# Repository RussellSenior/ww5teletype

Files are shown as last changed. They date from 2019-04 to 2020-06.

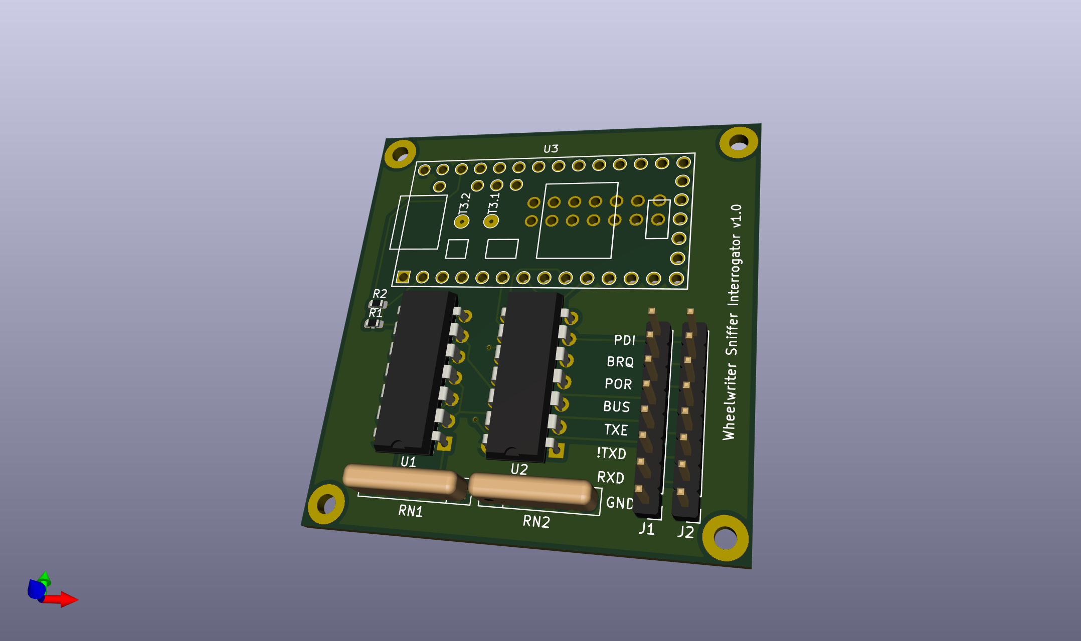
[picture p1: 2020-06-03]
hardware/reverse-engr/reverse-engr.png

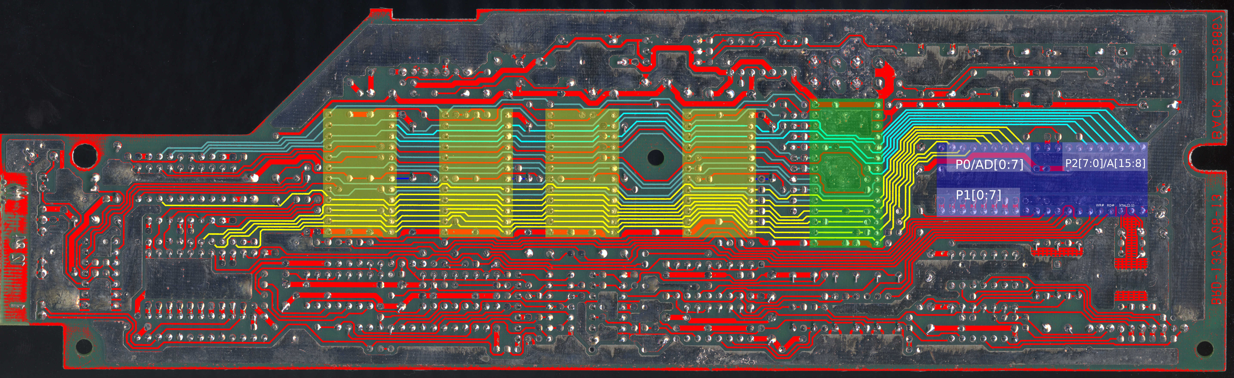
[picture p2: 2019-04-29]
img/wheelwriter_5_pcb_tracing_in_progress.jpg

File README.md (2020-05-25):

Exploration of the IBM Wheelwriter 5

This is a project motivated by a desire to create a daisywheel teletype, to give a 
similar experience to that of a Model 33ASR teletype, but with upper and lowercase 
characters. Thanks to Hugh Pyle and his fantastic [Twitch channel](https://www.twitch.tv/33asr) for the 
inspiration.  Thanks also to Chris Gregg and his project:
https://github.com/tofergregg/IBM-Wheelwriter-Hack and to this very similar project 
by Stephen Casner: https://github.com/IBM-1620/Junior.

The goal is to intercept user input from the keyboard and send it to a remote computer
and receive the echoed characters from the remote computer and send the corresponding
commands to the printing mechanism for hardcopy output.

I obtained an IBM Wheelwriter 5 from the Tektronix Surplus Store (open two days a month,
first and third Thursdays, from 2pm to 4pm) on the Beaverton Oregon campus of Tektronix. 
This typewriter came with the parallel port option, which hangs on the back of the case
and interfaces by a 6 (or 7?) pin bus. The cost of the typewriter was $25. I purchased 
two new-in-box ribbon cartridges from the same location for $0.50 each.

Following the lead of Chris Gregg, I began by putting a logic analyzer on the "bus" pin
between the keyboard controller board near the front of the typewriter and the motor 
control board in the rear of the typewriter and watching the response to keystrokes.

The keyboard controller board uses an Intel 8031 (romless version of the venerable 8051).
Reading the MCS-51 MICROCONTROLLER FAMILY USER’S MANUAL from Intel, it appears that the 
interboard communication takes place using a UART signaling but with the wrinkle that
both transmit and receive occur on the same wire. It appears that the UART is placed in 
the so-called "mode 2", which uses a 9-bit message, lsb first, where a one in the ninth bit 
indicates a corresponding target device (specified by the normal 8 bits) on the bus should 
listen to the message. Each message is ACK'd with nine bits of zero, presumably by the 
target device. Communication is at 1/64 of the crystal oscillator speed of 12MHz, which 
works out to 187500 baud (the logic analyzer, a Saleae clone using pulseview of the Sigrok
project, estimated the baud rate was 187060, which is very close, within 1/4%).

My original plan was to man-in-the-middle this serial bus wire, intercepting the commands 
coming from the keyboard controller board, decoding them, and sending a corresponding 
ASCII character (or, perhaps, string) to the remote computer over a normal 8N1 like UART,
receiving a ASCII back from the remote computer and injecting the corresponding commands
on the split bus.  However, due to some challenges, this is easier said than done:

Amongst other things, the keyboard has no "Control" key, therefore it becomes necessary
to hijack another key to act on its behalf. The most obvious candidate is the "Code"
key, which sits on the space bar row, to the left of the space bar. The difficulty arises
when you discover that the combination of "Code" and some other keys generates a rather 
complex series of commands, which would need to be decoded. This isn't impossible, but it
seems like a lot of complex work.

A second alternative, one taken by Stephen Casner for the IBM 1620 Junior project, is to 
intercept key presses directly from the FFC cables coming from the keyboard itself, and decode
the matrix. The corresponding ASCII characters can be sent to the remote computer and a fake
keyboard can be presented to the keyboard controller board.  I need to learn more about how
the keyboard matrix works.

One desirable feature is the ability to return to a "local" (vs "line") mode, where normal
typewriter functionality is restored, either through software or perhaps a hardware switch.

Thanks to the able assistance of [Jared Boone](https://github.com/jboone) of [ShareBrained Technology](https://www.sharebrained.com/), of Chronulator and 
PortaPack fame, I was able to obtain dumps of the off-chip ROMs for the keyboard controller 
and printer option boards (there are some other ROMs, but they seem less important).  They
can be found in the rom subdirectory. The motor control ROM would also be interesting, but
they are more obfuscated than even the keyboard controller board.

One oddity found in the disassembled firmware so far, it's not clear where the UART is 
configured in the keyboard controller firmware. I see references to the control register 
SCON in the printer board firmware, but not in the keyboard controller. Setting up the 
9-bit serial mode must require twiddling that register, so wtf?

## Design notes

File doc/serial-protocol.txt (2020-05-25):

There is a ribbon cable connecting the function board in front to the printer board in back. The pins are labelled (left to right):

 * +12
 * PDI
 * BRQ
 * BUS
 * GND
 * POR
 * +5

+12 carries a 12V supply, and +5 carries a 5V supply. GND is Ground. So much for the obvious. BUS carries serial communication between the boards. POR is Power On Reset, is low for a while at power on while things are initialized. BRQ is probably Bus Request. It is only asserted (LOW) when the PC Printer Option is attached, and only when the 0x140 byte is transmitted. PDI is a complete mystery so far.

The printer board also has a 0.1-inch pin header for connecting an external option card. In my case, I have a PC Printer Option card that came with the typewriter. The pins on this connector are labelled:

 * +5
 * GND
 * BUS
 * BRQ
 * POR
 * +34
 * PDI

Observations:

 * The protocol on the BUS wire is a 9-bit serial, apparently the so-called "mode 2" referred to in the Intel 8051 documentation: http://datasheets.chipdb.org/Intel/MCS51/MANUALS/27238302.PDF
 * The 9-bit bytes with the most-significant bit set indicate that the remaining bits are a processor address intended to listen to the commands that follow, so the many 0x121 are just spamming an announcement that the microprocessor on the bus that thinks of itself as 0x21 should pay attention, and that other microprocessors can sleep (only looking for the most-significant bit to see if they should check the address again). One can reasonably deduce that 0x21 is the address of the motor controller board. All other bytes, where the 9th bit is not set, are commands or arguments.
 * horizontal motion is typically measured in microsteps, 1/120th of an inch;
 * carriage motion is most often commanded relative to the current position, so it is necessary for the programming issuing commands to maintain a notion of where the carriage is located for carriage returns and to prevent venturing off the right end;
 * 0x03 takes two arguments, the first byte being the absolute rotation of the daisy wheel (between 0 and 0x60, inclusive) to strike, and the second byte being the number of microsteps to move the carriage to the right afterwards;
 * 0x04 seems to be similar to 0x03, except that it causes the ribbon positioning motor to rotate the rubout tape into position to be struck instead of the normal ribbon;
 * 0x05 command is a platen positioning command, the most significant bit of the single byte argument is a direction bit (1 for up, 0 for down), the rest indicate the magnitude of motion in 1/96ths of an inch;
 * 0x06 command is a carriage positioning command, taking two byte arguments: the most significant bit of the first byte indicates the direction (1 to move the carriage right, 0 to move the carriage to the left), the remaining bits indicate the number of microsteps (1/120th of an inch) to move horizontally;
 * 0x09 command followed by the single byte argument 0x04 seems to turn on underlining;
 * 0x09 command followed by the single byte argument 0x00 seems to turn off underlining;
 * 0x0B commands seem to not result in any actions, maybe a "rest" or "request status" command (we sometimes see non-zero replies to it);
 * 0x0C commands appear after a rubout operation;
 * 0x0D commands appear in connection with:
  * 0x05 during rubout;
  * 0x04 during backspace;
  * 0x07 during carriage return;
  * 0x0a during tab resolution;
  * 0x12 during tab set;
 * 0x0E commands appear in association with "code" related key presses;

 * A carriage return with a Courier 15 printwheel installed emitted an argument of 0x0c (decimal 12), which equates to 8 lines per inch. I also discovered that after an 0x03 command (i.e. printing/advancing), another addressing byte (0x121) was needed before a 0x05 (or probably any other command) was recognized or acknowledged.

 * With the PC Printer option attached, after putting the wheelwriter into Printer On mode (which is associated with its own bus traffic), sending data from a PC over /dev/usb/lp1 (which is line buffered and isn't printed until a ^M is sent), I see the following sequence:
  * about 16.8us before the first character, BRQ is pulled low, then the 9-bit character 0x140 appears;
  * about 87.5us after the start bit, BRQ is deasserted (goes HI again);
  * generally speaking BRQ going LO seems to be associated with the 0x140 byte generally, sometimes including other bytes.
  * as mentioned above the high bit being set implies an address in the lower 8 bits, in this case 0x40;
  * 0x114 appears (unless otherwise indicated, 0x00 replies are implied);
  * 0x005;
  * 0x006;
  * 0x110;
  * 0x140 (with BRQ LO);
  * 0x114;
  * 0x003;
  * 0x067;
  * 0x110;
  * 0x141;
  * 0x083 (reply 0x001);
  * 0x141;
  * 0x00E (BRQ goes LO in the middle of transmission);
  * 0x0E7;
  * 0x140 (the BRQ goes HI again);
  * 0x114;
  * 0x003;
  * 0x0E7;
  * 0x110;
  * 0x121;
  * 0x00B;
  * 0x141;
  * 0x083 (reply 0x001);
  * 0x140 (with BRQ LO during the byte);
  * 0x114;
  * 0x003;
  * 0x0C9;
  * 0x124;
  * 0x000 (reply: 0x025);
  * 0x110;
  * 0x141;
  * 0x083 (reply: 0x001);
  * 0x121;
  * 0x00B;
  * 0x140 (with BRQ LO during the byte);
  * 0x114;
  * 0x003;
  * 0x05F;
  * 0x110;
  * 0x141;
  * 0x083 (reply: 0x001);
  * 0x121;
  * 0x00B;
  * 0x140 (with BRQ LO as before);
  * 0x114;
  * 0x003;
  * 0x025;
  * 0x110;
  * 0x141;
  * 0x083 (reply: 0x001);
  * 0x140 (with BRQ LO as before);
  * 0x114;
  * 0x003;
  * 0x0A5;
  * 0x110;
  * 0x121;
  * 0x00B;
  * 0x141;
  * 0x003;
  * 0x014 (character H);
  * 0x008 (advance 8 microsteps);
  * 0x140 (with BRQ LO as before);
  * 0x124;
  * 0x003;
  * 0x014 (character H);
  * 0x008 (advance 8 microsteps); 
  * 0x110;
  * 0x141;
  * 0x083 (reply: 0x001);
  * 0x140 (with BRQ LO as before);
  * 0x114;
  * 0x003;
  * 0x0DF;
  * 0x110;
  * 0x141;
  * 0x083 (reply: 0x001);
  * 0x121 (BRQ goes LO afterwards, before 0x000 ack, long delay before ack);
  * 0x00B (reply: 0x007);
  * 0x140 (BRQ goes HI afterwards);
  * 0x114;
  * 0x003;
  * 0x012;
  * 0x110;
  * 0x141;
  * 0x083 (reply: 0x001);
  * 0x140 (with BRQ LO as before);
  * 0x114;
  * 0x003;
  * 0x092;
  * 0x110;
  * 0x121;
  * 0x00B (reply: 0x007);
  * 0x141;
  * 0x003;
  * 0x060 (character 'e'?);
  * 0x008;
  * 0x140 (with BRQ LO);
  * 0x124;
  * 0x003;
  * 0x060 (character 'e');
  * 0x008 (advance 8 microsteps);
  * 0x110;
  * 0x141;
  * 0x083 (reply: 0x001);
  * 0x140 (with BRQ LO as before);
  * 0x114;
  * 0x003; 
  * 0x034;
  * 0x110;
  * 0x141;
  * 0x083 (reply: 0x001);
  * 0x140 (with BRQ LO as before);
  * 0x114;
  * 0x003;
  * 0x0B4;
  * 0x110;
  * 0x121;
  * 0x00B (reply: 0x007);
  * 0x141;
  * 0x003;
  * 0x009 (character 'l');
  * 0x008 (advance 8 microsteps);
  * 0x140 (with BRQ LO as before);
  * 0x124;
  * 0x003;
  * 0x009 (character 'l');
  * 0x008 (advance 8 microsteps);
  * 0x110;
  * 0x141;
  * 0x083 (reply: 0x001);
  * 0x140 (with BRQ LO as before);
  * 0x114;
  * 0x003;
  * 0x034;
  * 0x110;
  * 0x141;
  * 0x083 (reply: 0x001);
  * 0x140 (with BRQ LO as before);
  * 0x114;
  * 0x003;
  * 0x0B4;
  * 0x110;
  * 0x121;
  * 0x00B (reply: 0x007);
  * 0x141;
  * 0x003;
  * 0x009 (character 'l');
  * 0x008 (advance 8 microsteps);
  * 0x140 (with BRQ LO as before);
  * 0x124;
  * 0x003;
  * 0x009 (character 'l');
  * 0x008 (advance 8 microsteps);
  * 0x110;
  * 0x141;
  * 0x083 (reply: 0x001);
  * 0x140 (with BRQ LO as before);
  * 0x114;
  * 0x003;
  * 0x032;
  * 0x110;
  * 0x141;
  * 0x083 (reply: 0x001);
  * 0x140 (with BRQ LO as before);
  * 0x114;
  * 0x003;
  * 0x0B2;
  * 0x110;
  * 0x121;
  * 0x00B (reply: 0x007);
  * 0x141;
  * 0x003;
  * 0x05F (character 'o');
  * 0x008 (advance 8 microsteps);
  * 0x140 (with BRQ LO as before);
  * 0x124;
  * 0x003;
  * 0x05F character 'o');
  * 0x008 (advance 8 microsteps);
  * 0x110;
  * 0x141;
  * 0x083 (reply: 0x001);
  * 0x140 (with BRQ LO as before);
  * 0x114;
  * 0x003;
  * 0x02E;
  * 0x110;
  * 0x141;
  * 0x083 (reply: 0x001);
  * 0x140 (with BRQ LO as before);
  * 0x114;
  * 0x003;
  * 0x0AE;
  * 0x110;
  * 0x121;
  * 0x00B (reply: 0x007);
  * 0x141;
  * 0x003;
  * 0x00C (character ',');
  * 0x008 (advance 8 microsteps);
  * 0x140 (with BRQ LO as before);
  * 0x124;
  * 0x003;
  * 0x00C (character ',');
  * 0x008 (advance 8 microsteps);
  * 0x110;
  * 0x141;
  * 0x083 (reply: 0x001);
  * 0x140 (with BRQ LO as before);
  * 0x114;
  * 0x003;
  * 0x047;
  * 0x110;
  * 0x141;
  * 0x083 (reply: 0x001);
  * 0x121;
  * 0x00B (reply: 0x007);
  * 0x140 (with BRQ LO as before);
  * 0x114;
  * 0x003;
  * 0x0C7;
  * 0x110;
  * 0x141;
  * 0x003;
  * 0x000 (character ' ');
  * 0x008 (advance 8 microsteps);
  * 0x141;
  * 0x083 (reply: 0x001);
  * 0x140 (with BRQ LO as before);
  * 0x114;
  * 0x003;
  * 0x05F;
  * 0x110;
  * 0x141;
  * 0x083 (reply: 0x001);
  * 0x121;
  * 0x00B (reply: 0x007);
  * 0x140 (with BRQ LO as before);
  * 0x114;
  * 0x003;
  * 0x00A;
  * 0x110;
  * 0x141;
  * 0x083 (reply: 0x001);
  * 0x140 (with BRQ LO as before);
  * 0x114;
  * 0x003;
  * 0x08A;
  * 0x110;
  * 0x121;
  * 0x00B (reply: 5);
  * 0x141;
  * 0x003;
  * 0x029 (character 'W');
  * 0x008 (advance 8 microsteps);
  * 0x140 (BRQ LO);
  * 0x124;
  * 0x006;
  * 0x080;
  * 0x008;
  * 0x124;
  * 0x003;
  * 0x029 (character 'W');
  * 0x008 (advance 8 microsteps);
  * 0x110;
  * 0x141;
  * 0x083 (reply: 0x001);
  * 0x140 (BRQ goes HI afterwards);
  * 0x114;
  * 0x003;
  * 0x0DF;
  * 0x110;
  * 0x141;
  * 0x083 (reply: 0x001);
  * 0x121 (BRQ goes LO afterwards);
  * 0x00B (reply: 0x007);
  * 0x140 (BRQ goes HI afterwards);
  * 0x114;
  * 0x003;
  * 0x032;
  * 0x110;
  * 0x141;
  * 0x083 (reply: 0x001);
  * 0x140 (with BRQ LO as before);
  * 0x114;
  * 0x003;
  * 0x0B2;
  * 0x110;
  * 0x121;
  * 0x00B (reply: 0x007);
  * 0x141;
  * 0x003;
  * 0x05F (character 'o');
  * 0x008 (advance 8 microsteps);
  * 0x140 (with BRQ LO as before);
  * 0x124;
  * 0x003;
  * 0x05F (character 'o');
  * 0x008 (advance 8 microsteps);
  * 0x110;
  * 0x141;
  * 0x083 (reply: 0x001);
  * 0x140 (with BRQ LO as before);
  * 0x114;
  * 0x003;
  * 0x01A;
  * 0x110;
  * 0x141;
  * 0x083 (reply: 0x001);
  * 0x140 (with BRQ LO as before);
  * 0x114;
  * 0x003;
  * 0x09A;
  * 0x110;
  * 0x121;
  * 0x00B (reply: 0x007);
  * 0x141;
  * 0x003;
  * 0x003 (character 'r');
  * 0x008 (advance 8 microsteps);
  * 0x140 (with BRQ LO as before);
  * 0x124;
  * 0x003;
  * 0x003 (character 'r');
  * 0x008 (advance 8 microsteps);
  * 0x110;
  * 0x141;
  * 0x083 (reply: 0x001);
  * 0x140 (with BRQ LO as before);
  * 0x114;
  * 0x003;
  * 0x034;
  * 0x110;
  * 0x141;
  * 0x083 (reply: 0x001);
  * 0x140 (with BRQ LO as before);
  * 0x114;
  * 0x003;
  * 0x0B4;
  * 0x110;
  * 0x121;
  * 0x00B (reply: 0x007);
  * 0x141;
  * 0x003;
  * 0x009 (character 'l');
  * 0x008 (advance 8 microsteps);
  * 0x140 (with BRQ LO as before);
  * 0x124;
  * 0x003;
  * 0x009 (character 'l');
  * 0x008 (advance 8 microsteps);
  * 0x110;
  * 0x141;
  * 0x083 (reply: 0x001);
  * 0x140 (with BRQ LO as before);
  * 0x114;
  * 0x003;
  * 0x014;
  * 0x110;
  * 0x141;
  * 0x083 (reply: 0x001);
  * 0x140 (with BRQ LO as before);
  * 0x114;
  * 0x003;
  * 0x094;
  * 0x110;
  * 0x121;
  * 0x00B (reply: 0x007);
  * 0x141;
  * 0x003;
  * 0x007 (character 'd');
  * 0x008 (advance 8 microsteps);
  * 0x140 (with BRQ LO, HI and the LO again);
  * 0x124;
  * 0x003;
  * 0x007 (character 'd');
  * 0x008 (advance 8 microsteps);
  * 0x110;
  * 0x141;
  * 0x083 (reply: 0x001);
  * 0x140 (then BRQ goes HI afterwards);
  * 0x110;
  * 0x140 (with BRQ LO as before);
  * 0x114;
  * 0x003;
  * 0x05F;
  * 0x110;
  * 0x141;
  * 0x083 (reply: 0x001);
  * 0x121 (BRQ goes LO afterwards);
  * 0x00B (reply: 0x007);
  * 0x140 (then BRQ goes HI afterwards);
  * 0x114;
  * 0x003;
  * 0x001;
  * 0x110;
  * 0x141;
  * 0x083 (reply: 0x001);
  * 0x140 (with BRQ LO as before);
  * 0x114;
  * 0x003;
  * 0x081;
  * 0x110;
  * 0x121;
  * 0x00B (reply: 0x007);
  * 0x141;
  * 0x003;
  * 0x049 (character '!');
  * 0x008 (advance 8 microsteps);
  * 0x140 (with BRQ LO as before);
  * 0x124;
  * 0x003;
  * 0x049 (character '!');
  * 0x008 (advance 8 microsteps);
  * 0x110;
  * 0x141;
  * 0x083 (reply: 0x001);
  * 0x140 (with BRQ LO as before);
  * 0x114;
  * 0x003;
  * 0x056;
  * 0x110;
  * 0x141;
  * 0x083 (reply: 0x001);
  * 0x121 (BRQ goes LO afterwards);
  * 0x00B (reply: 0x007);
  * 0x140 (BRQ goes HI afterwards);
  * 0x114;
  * 0x003;
  * 0x0D6;
  * 0x110;
  * 0x141;
  * 0x00D;
  * 0x007;
  * 0x141;
  * 0x006;
  * 0x000;
  * 0x068;
  * 0x141;
  * 0x005;
  * 0x08C;
  * 0x140 (with BRQ LO, then HI, then LO again);
  * 0x124;
  * 0x006;
  * 0x000;
  * 0x068;
  * 0x124;
  * 0x005;
  * 0x08C;

  * 0x124;
  * 0x00B (reply: 0x014); [repeats 11 times at about 10.98ms intervals]

  * 0x124;
  * 0x00B (reply: 0x004); [repeats 16 times at about 10.92ms intervals]

  * 0x124;
  * 0x00B;
  * 0x110;
  * 0x141;
  * 0x083 (reply: 0x001);
  * 0x140 (BRQ goes HI afterwards);
  * 0x114;
  * 0x003;
  * 0x067;
  * 0x110;
  * 0x141;
  * 0x083 (reply: 0x001);
  * 0x141;
  * 0x00E (BRQ goes LO afterwards);
  * 0x0E7;
  * 0x140 (BRQ goes HI aftwerwards);
  * 0x114;
  * 0x003;
  * 0x049;
  * 0x110;
  * 0x121;
  * 0x00B;
  * 0x141;
  * 0x083 (reply: 0x001);
  * 0x141;
  * 0x00E (BRQ goes LO during);
  * 0x0C9;
  * 0x140 (BRQ goes HI aftwerwards);
  * 0x114;
  * 0x003;
  * 0x0C9;
  * 0x110;
  * 0x141;
  * 0x083 (reply: 0x001);
  * 0x121;
  * 0x00B;
  * 0x140 (with BRQ pulled LO);
  * 0x114;
  * 0x003;
  * 0x0E7;
  * 0x110;
  * 0x141;
  * 0x083 (reply: 0x001);
  * 0x121;
  * 0x00B;
  * 0x140 (with BRQ pulled LO);
  * 0x114;
  * 0x003;
  * 0x067;
  * 0x110;
  * 0x141;
  * 0x083 (reply: 0x001);
  * 0x141;
  * 0x00E (BRQ goes LO afterwards);
  * 0x0E7;
  * 0x140 (BRQ goes HI aftwerwards);
  * 0x114;
  * 0x003;
  * 0x0E7;
  * 0x110;
  * 0x121;
  * 0x00B;
  * 0x141;
  * 0x083 (reply: 0x001);
  * 0x140 (with BRQ pulled LO);
  * 0x114;
  * 0x003;
  * 0x0C9;
  * 0x124;
  * 0x000 (reply: 0x025);
  * 0x114;
  * 0x005;
  * 0x00E;
  * 0x110;
  * 0x141;
  * 0x083 (reply: 0x001);
  * 0x121;
  * 0x00B;

 * While printing from PC Printer Option, the "Ready" LED on the keyboard, turns off. while Active and Online remain on.

 * With Printer On (Active, Online, Ready LEDs on) to Offline (Active and Ready LEDs on), the following sequence appears on the bus:
  * 0x141;
  * 0x082;
  * 0x067 (reply: 0x001);
  * 0x141;
  * 0x082;
  * 0x020 (reply: 0x001);
  * 0x140 (with BRQ pulled LO);
  * 0x114;
  * 0x005;
  * 0x00A;
  * 0x114;
  * 0x003;
  * 0x067;
  * 0x110;
  * 0x141;
  * 0x083 (reply: 0x001);
  * 0x141;
  * 0x00E (BRQ goes LO afterwards);
  * 0x0E7;
  * 0x140 (BRQ goes HI afterwards);
  * 0x114;
  * 0x003;
  * 0x0E7;
  * 0x110;
  * 0x121;
  * 0x00B;
  * 0x141;
  * 0x083 (reply: 0x001);
  * 0x140 (with BRQ pulled LO);
  * 0x114;
  * 0x003;
  * 0x0C9;
  * 0x124;
  * 0x007;
  * 0x110;
  * 0x141;
  * 0x083 (reply: 0x001);
  * 0x121;
  * 0x00B;
  * 0x141;
  * 0x082;
  * 0x0A0 (reply: 0x001);
  * 0x141;
  * 0x082;
  * 0x0E7 (reply: 0x001);

 * Printer to Online (opposite of previous):
  * 0x141;
  * 0x082;
  * 0x067 (reply: 0x001);
  <delay probably from Code press to Onlne press>
  * 0x141;
  * 0x082;
  * 0x020 (reply: 0x001);
  * 0x140 (with BRQ pulled LO);
  * 0x114;
  * 0x005;
  * 0x00E;
  * 0x114;
  * 0x005;
  * 0x006;
  * 0x114;
  * 0x003;
  * 0x067;
  * 0x110;
  * 0x141;
  * 0x083 (reply: 0x001);
  * 0x141;
  * 0x00E (BRQ goes LO during);
  * 0x0E7;
  * 0x140 (BRQ returns HI afterwards);
  * 0x114;
  * 0x003;
  * 0x0E7;
  * 0x110;
  * 0x121;
  * 0x00B;
  * 0x141;
  * 0x083 (reply: 0x001);
  * 0x140 (with BRQ pulled LO);
  * 0x114;
  * 0x003;
  * 0x0C9;
  * 0x124;
  * 0x007;
  * 0x114;
  * 0x005;
  * 0x00E;
  * 0x110;
  * 0x141;
  * 0x083 (reply: 0x001);
  * 0x121;
  * 0x00B;
  * 0x141;
  * 0x082;
  * 0x0A0 (reply: 0x001);
  * 0x141;
  * 0x082;
  * 0x0E7 (reply: 0x001);

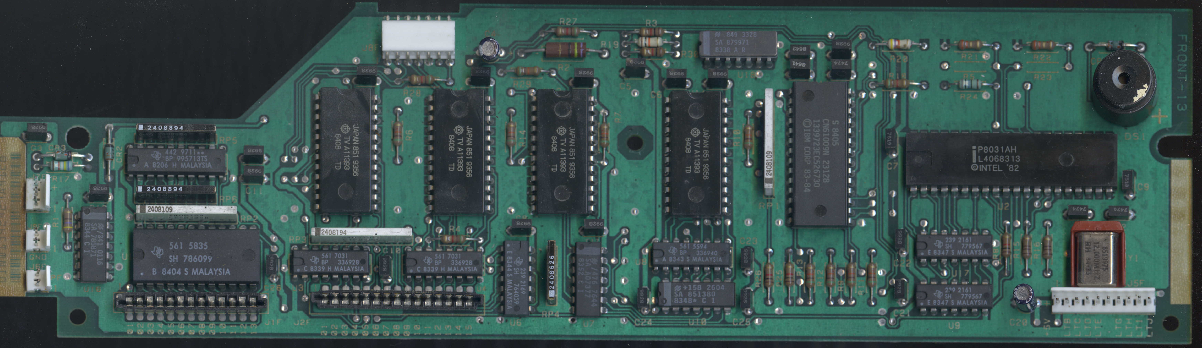
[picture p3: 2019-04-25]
img/keyboard-controller-front.jpg

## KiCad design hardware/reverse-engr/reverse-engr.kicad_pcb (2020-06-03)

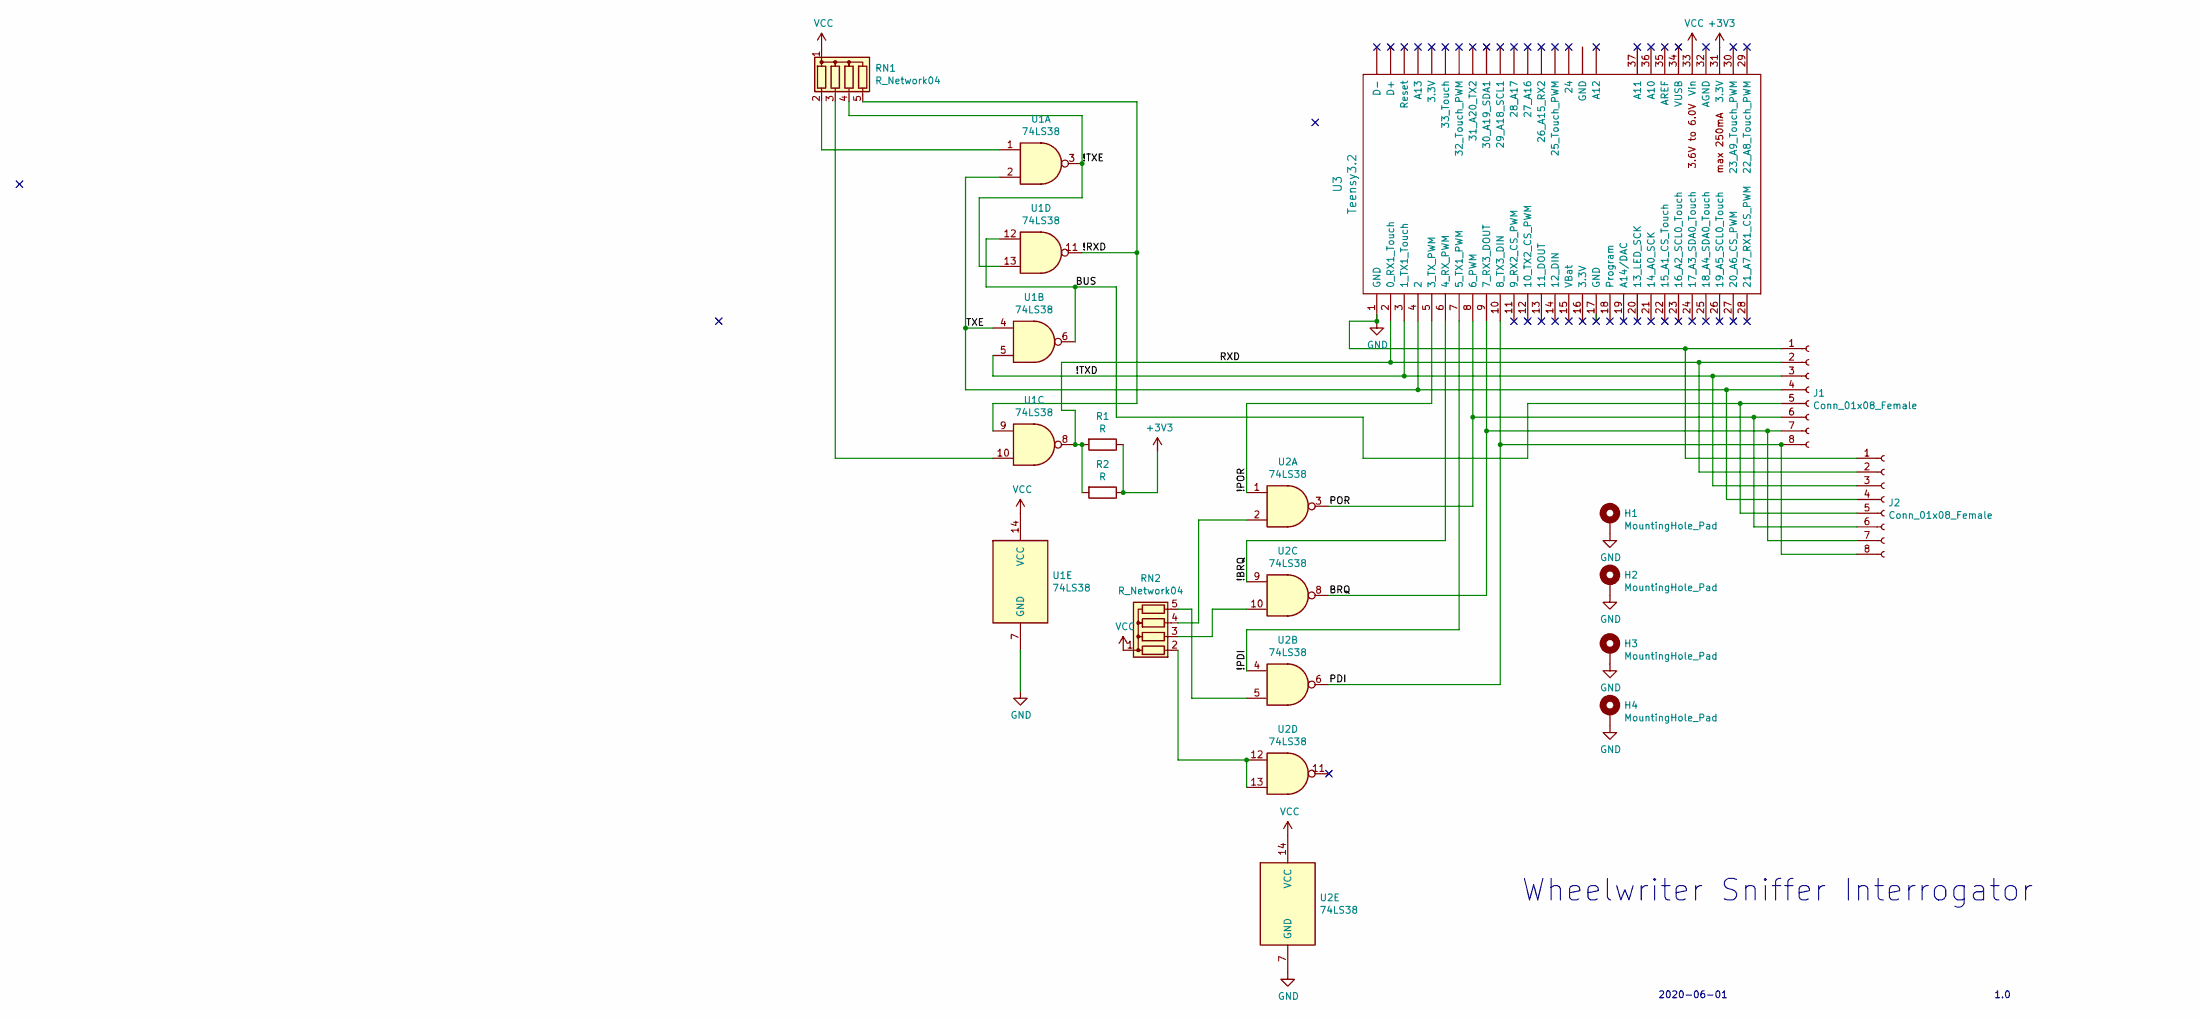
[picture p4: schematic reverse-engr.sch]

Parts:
H1, H2, H3, H4: MountingHole_Pad; MountingHole_2.2mm_M2_Pad
J1, J2: Conn_01x08_Female; PinHeader_1x08_P2.54mm_Vertical
R1, R2: R; R_0603_1608Metric
RN1, RN2: R_Network04; R_Array_SIP5
U1, U2: 74LS38; DIP-14_W7.62mm
U3: Teensy3.2; Teensy30_31_32_LC

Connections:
+3V3: R1.1, R2.1, U3.31 (3.3V)
/!BRQ: U2.9, U3.6 (4_RX_PWM)
/!PDI: U2.4, U3.7 (5_TX1_PWM)
/!POR: U2.1, U3.5 (3_TX_PWM)
/!RXD: RN1.5 (R4), U1.9, U1.11
/!TXD: J1.3, J2.3, U1.5, U3.3 (1_TX1_Touch)
/!TXE: RN1.4 (R3), U1.3, U1.13
/BRQ: J1.7, J2.7, U2.8, U3.9 (7_RX3_DOUT)
/BUS: J1.5, J2.5, U1.6, U1.12
/PDI: J1.8, J2.8, U2.6, U3.10 (8_TX3_DIN)
/POR: J1.6, J2.6, U2.3, U3.8 (6_PWM)
/RXD: J1.2, J2.2, R1.2, R2.2, U1.8, U3.2 (0_RX1_Touch)
/TXE: J1.4, J2.4, U1.2, U1.4, U3.4 (2)
GND: H1.1, H2.1, H3.1, H4.1, J1.1, J2.1, U1.7 (GND), U2.7 (GND), U3.1 (GND)
unnamed: RN1.2 (R1), U1.1
unnamed: RN1.3 (R2), U1.10
unnamed: RN2.2 (R1), U2.12, U2.13
unnamed: RN2.3 (R2), U2.10
unnamed: RN2.4 (R3), U2.2
unnamed: RN2.5 (R4), U2.5
VCC: RN1.1 (common), RN2.1 (common), U1.14 (VCC), U2.14 (VCC), U3.33 (Vin)

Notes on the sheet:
Wheelwriter Sniffer Interrogator
1.0
2020-06-01

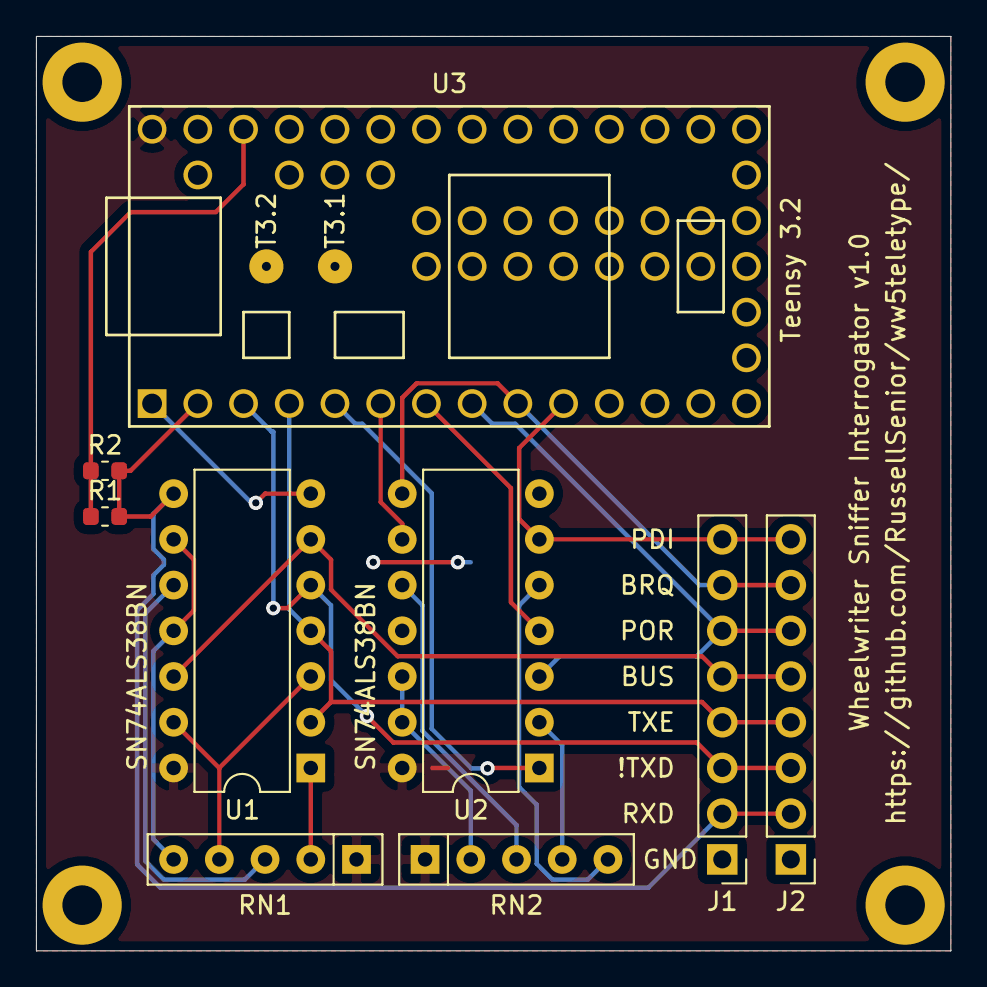
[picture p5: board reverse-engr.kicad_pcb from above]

Board: 2 copper layers, 50.8 x 50.8 mm, 13 parts (0 on the bottom side), 21 nets.

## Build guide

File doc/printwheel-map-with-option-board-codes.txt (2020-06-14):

wheeladdr
0x00	<space>	0x20
0x01	a	0x61	0x04
0x02	n	0x6e	0x27
0x03	r	0x72	0x1a
0x04	m	0x6d	0x26
0x05	c	0x63	0x16
0x06	s	0x73	0x0c
0x07	d	0x64	0x14
0x08	h	0x68	0x25
0x09	l	0x6c	0x34
0x0a	f	0x66	0x1c
0x0b	k	0x6b	0x2c
0x0c	,	0x2c	0x2e
0x0d	V	0x56	0x1e shift
0x0e	-	0x2d	0x38
0x0f	G	0x47	0x1d shift
0x10	U	0x55	0x22 shift
0x11	F	0x46	0x1c shift
0x12	B	0x42	0x1f shift
0x13	Z	0x5a	0x06 shift
0x14	H	0x48	0x25 shift
0x15	P	0x50	0x3a shift
0x16	)	0x29	0x39 shift
0x17	R	0x52	0x1a shift
0x18	L	0x4c	0x34 shift
0x19	S	0x53	0x0c shift
0x1a	N	0x4e	0x27 shift
0x1b	C	0x43	0x16 shift
0x1c	T	0x54	0x1b shift
0x1d	D	0x44	0x14 shift
0x1e	E	0x45	0x12 shift
0x1f	I	0x49	0x2a shift
0x20	A	0x41	0x04 shift
0x21	J	0x4a	0x24 shift
0x22	O	0x4f	0x32 shift
0x23	(	0x28	0x31 shift
0x24	M	0x4d	0x26 shift
0x25	.	0x2e	0x36 shift
0x26	Y	0x59	0x23 shift
0x27	,	0x2c	0x2e shift
0x28	/	0x2f	0x3f
0x29	W	0x57	0x0a shift
0x2a	9	0x39	0x31
0x2b	K	0x4b	0x2c shift
0x2c	3	0x33	0x11
0x2d	X	0x58	0x0e shift
0x2e	1	0x31	0x01
0x2f	2	0x32	0x09
0x30	0	0x30	0x39
0x31	5	0x35	0x18
0x32	4	0x34	0x19
0x33	6	0x36	0x20
0x34	8	0x38	0x29
0x35	7	0x37	0x21
0x36	*	0x2a	0x29 shift
0x37	$	0x24	0x19 shift
0x38	#	0x23	0x11 shift
0x39	%	0x25	0x18 shift
0x3a	^	0x5e	0x20 shift
0x3b	+	0x2b	0x28 shift
0x3c	`	0x60	0x00 
0x3d	@	0x40	0x09 shift
0x3e	Q	0x51	0x02 shift
0x3f	&	0x26	0x21 shift
0x40	]	0x5d	0x2b
0x41	[	0x5b	0x2b shift
0x42	\	0x5c	0x3e
0x43	|	0x7c	0x3e shift
0x44	~	0x7e	0x00 shift
0x45	<	0x3c	0x07
0x46	>	0x3e	0x07 shift
0x47	}	0x7d	0x3b
0x48	{	0x7b	0x3b shift
0x49	!	0x21	0x01 shift
0x4a	?	0x3f	0x3f shift
0x4b	"	0x22	0x3d shift
0x4c	'	0x27	0x3d
0x4d	=	0x3d	0x28
0x4e	:	0x3a	0x3c shift
0x4f	_	0x5f	0x38 shift
0x50	;	0x3b	0x3c
0x51	x	0x78	0x0e
0x52	q	0x71	0x02
0x53	v	0x76	0x1e
0x54	z	0x7a	0x06
0x55	w	0x77	0x0a
0x56	j	0x6a	0x24
0x57	.	0x2e	0x36
0x58	y	0x79	0x23
0x59	b	0x62	0x1f
0x5a	g	0x67	0x1d
0x5b	u	0x75	0x22
0x5c	p	0x70	0x3a
0x5d	i	0x69	0x2a
0x5e	t	0x74	0x1b
0x5f	o	0x6f	0x32
0x60	e	0x65	0x12

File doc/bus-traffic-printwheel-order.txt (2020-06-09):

0x140 0x00
0x114 0x00 0x05 0x00 0x06 0x00
0x110 0x00
0x140 0x00
0x114 0x00 0x03 0x00 0x67 0x00
0x110 0x00
0x141 0x00 0x83 0x01
0x141 0x00 0x0e 0x00 0xe7 0x00
0x140 0x00
0x114 0x00 0x03 0x00 0xe7 0x00
0x110 0x00
0x121 0x00 0x0b 0x00
0x141 0x00 0x83 0x01
0x140 0x00
0x114 0x00 0x03 0x00 0xc9 0x00
0x124 0x00 0x00 0x25
0x110 0x00
0x141 0x00 0x83 0x01
0x121 0x00 0x0b 0x00
0x140 0x00
0x114 0x00 0x03 0x00 0x47 0x00
0x110 0x00
0x141 0x00 0x83 0x01
0x121 0x00 0x0b 0x00
0x140 0x00
0x114 0x00 0x03 0x00 0xc7 0x00
0x110 0x00
0x141 0x00 0x0d 0x00 0x03 0x00
0x141 0x00 0x06 0x00 0x80 0x00 0x08 0x00
0x141 0x00 0x83 0x01
0x140 0x00
0x114 0x00 0x03 0x00 0x04 0x00
0x110 0x00
0x141 0x00 0x83 0x01
0x140 0x00
0x114 0x00 0x03 0x00 0x84 0x00
0x110 0x00
0x121 0x00 0x0b 0x00
0x141 0x00 0x03 0x00 0x01 0x00 0x08 0x00
0x140 0x00
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

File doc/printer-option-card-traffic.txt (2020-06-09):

Watching traffic while operating the PC Printer Option card is complex.

Power on with printer option attached:

0x121 0x00 0x00 0x25
0x121 0x00 0x01 0x10
0x121 0x00 0x09 0x00 0x00 0x00
0x121 0x00 0x0d 0x00 0x12 0x00
0x121 0x00 0x06 0x00 0x80 0x00 0x00 0x00
0x121 0x00 0x0d 0x00 0x09 0x00
0x121 0x00 0x06 0x00 0x80 0x00 0x00 0x00
0x121 0x00 0x0a 0x00 0x00 0x00
0x121 0x00 0x07 0x00
0x121 0x00 0x0c 0x00 0x01 0x00
0x140 0x00
0x114 0x00 0x00 0x20
0x110 0x00

Toggling printer card on:

0x121 0x00 0x0e 0x00 0xe7 0x00
0x121 0x00 0x0b 0x00
0x121 0x00 0x0e 0x00 0x98 0x00
0x121 0x00 0x0b 0x00
0x140 0x00
0x124 0x00 0x07 0x00
0x114 0x00 0x0f 0x00 0x20 0x00
0x124 0x00 0x0e 0x00 0x6e 0x00
0x114 0x00 0x01 0x00
0x110 0x00
0x121 0x00 0x0c 0x00 0xc0 0x00
0x140 0x00
0x110 0x00
0x121 0x00 0x09 0x00 0x00 0x00
0x121 0x00 0x05 0x00 0x8c 0x00
0x121 0x00 0x0d 0x00 0x07 0x00
0x121 0x00 0x06 0x00 0x80 0x00 0x00 0x00
0x140 0x00
0x114 0x00 0x03 0x00 0x52 0x00
0x110 0x00
0x141 0x00 0x83 0x01
0x121 0x00 0x0b 0x00
0x140 0x00
0x114 0x00 0x03 0x00 0xd2 0x00
0x110 0x00
0x121 0x00 0x05 0x00 0x06 0x00
0x141 0x00 0x82 0x00 0x67 0x01
0x141 0x00 0x83 0x01
0x121 0x00 0x0b 0x10
0x140 0x00
0x114 0x00 0x03 0x00 0x52 0x00
0x110 0x00
0x141 0x00 0x83 0x01
0x121 0x00 0x0b 0x10
0x140 0x00
0x114 0x00 0x03 0x00 0xd2 0x00
0x114 0x00 0x0f 0x00 0x40 0x00
0x110 0x00
0x141 0x00 0x05 0x00 0x06 0x00
0x140 0x00
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

Printing the first 10 characters on the wheel:

0x140 0x00
0x114 0x00 0x05 0x00 0x06 0x00
0x110 0x00
0x140 0x00
0x114 0x00 0x03 0x00 0x67 0x00
0x110 0x00
0x141 0x00 0x83 0x01
0x141 0x00 0x0e 0x00 0xe7 0x00
0x140 0x00
0x114 0x00 0x03 0x00 0xe7 0x00
0x110 0x00
0x121 0x00 0x0b 0x00
0x141 0x00 0x83 0x01
0x140 0x00
0x114 0x00 0x03 0x00 0xc9 0x00
0x124 0x00 0x00 0x25
0x110 0x00
0x141 0x00 0x83 0x01
0x121 0x00 0x0b 0x00
0x140 0x00
0x114 0x00 0x03 0x00 0x04 0x00
0x110 0x00
0x141 0x00 0x83 0x01
0x140 0x00
0x114 0x00 0x03 0x00 0x84 0x00
0x110 0x00
0x121 0x00 0x0b 0x00
0x141 0x00 0x0c 0x00 0x81 0x00
0x140 0x00
0x114 0x00 0x05 0x00 0x06 0x00
0x110 0x00
0x141 0x00 0x03 0x00 0x01 0x00 0x08 0x00
0x140 0x00
0x124 0x00 0x03 0x00 0x01 0x00 0x08 0x00
0x110 0x00
0x141 0x00 0x83 0x01
0x140 0x00
0x114 0x00 0x03 0x00 0x27 0x00
0x110 0x00
0x141 0x00 0x83 0x01
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

Toggle the printer option offline:

0x141 0x00 0x82 0x00 0x67 0x01
0x141 0x00 0x82 0x00 0x18 0x01
0x141 0x00 0x82 0x00 0x98 0x01
0x140 0x00
0x114 0x00 0x05 0x00 0x02 0x00
0x114 0x00 0x03 0x00 0x67 0x00
0x110 0x00
0x141 0x00 0x83 0x01
0x141 0x00 0x0e 0x00 0xe7 0x00
0x140 0x00
0x114 0x00 0x03 0x00 0xe7 0x00
0x110 0x00
0x121 0x00 0x0b 0x00
0x141 0x00 0x83 0x01
0x140 0x00
0x114 0x00 0x03 0x00 0xc9 0x00
0x124 0x00 0x07 0x00
0x110 0x00
0x141 0x00 0x83 0x01
0x121 0x00 0x0b 0x00
0x140 0x00
0x114 0x00 0x03 0x00 0x67 0x00
0x110 0x00
0x141 0x00 0x83 0x01
0x141 0x00 0x0e 0x00 0xe7 0x00
0x140 0x00
0x114 0x00 0x03 0x00 0xe7 0x00
0x110 0x00
0x121 0x00 0x0b 0x00
0x141 0x00 0x83 0x01
0x140 0x00
0x114 0x00 0x03 0x00 0xc9 0x00
0x124 0x00 0x00 0x25
0x110 0x00
0x141 0x00 0x83 0x01
0x121 0x00 0x0b 0x00
0x140 0x00
0x114 0x00 0x03 0x00 0x56 0x00
0x110 0x00
0x141 0x00 0x83 0x01
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

The 0x140 and 0x110 appear to be involved with token passing between
the function board and the pc printer option. The 0x140 is always
associated with BRQ going low, perhaps the option card requesting the
bus, and perhaps 0x110 is handing the token back, or maybe even the
opposite.

0x124 and 0x141 commands look like normal 0x121 commands as far as
coding. However both versions are sent. This might be because one of
them is for effect and the other is to keep the function board in the
loop regarding the position of the carriage.  All the 0x141 codes look
familiar except for 0x141 0x83 with a consistent return value of 0x01.

0x114 commands are not familiar looking, except that the 0x03 command
seem to come approximately in pairs with the second version turning on
the high bit in arg1.

Okay, here's the current theory:

  the option card pulls BRQ low
  function card sends 0x140
  option card releases BRQ (pulled back high)
  option card returns 0x00
  option card sends some commands on the bus
  when finished, option card sends 0x110 to release the bus

In order to really determine the direction of these I need some kind
of circuit to tell which direction the pull downs are coming
from.

Pulling BRQ low manually, I get a gigantic stream of continuous
alternating 0x140's and 0x110's, which is consistent with my theory.

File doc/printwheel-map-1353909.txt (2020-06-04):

wheeladdr
0x00	<space>	0x20
0x01	a	0x61
0x02	n	0x6e
0x03	r	0x72
0x04	m	0x6d
0x05	c	0x63
0x06	s	0x73
0x07	d	0x64
0x08	h	0x68
0x09	l	0x6c
0x0a	f	0x66
0x0b	k	0x6b
0x0c	,	0x2c
0x0d	V	0x56
0x0e	-	0x2d
0x0f	G	0x47
0x10	U	0x55
0x11	F	0x46
0x12	B	0x42
0x13	Z	0x5a
0x14	H	0x48
0x15	P	0x50
0x16	)	0x29
0x17	R	0x52
0x18	L	0x4c
0x19	S	0x53
0x1a	N	0x4e
0x1b	C	0x43
0x1c	T	0x54
0x1d	D	0x44
0x1e	E	0x45
0x1f	I	0x49
0x20	A	0x41
0x21	J	0x4a
0x22	O	0x4f
0x23	(	0x28
0x24	M	0x4d
0x25	.	0x2e
0x26	Y	0x59
0x27	,	0x2c
0x28	/	0x2f
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

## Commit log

2019-04-25 first check-in
    includes images of the front and back (flipped) of the keyboard controller
    board.
2019-04-29 add more information, including:
    * ROM dumps from keyboard and parallel printing controller 8031 boards
    * disassembly of those ROM dumps
    * a color coded pcb trace image (still some traces hidden by chips)
2020-05-25 add some bus traces from pulseview
2020-06-03 add kicad sniffer circuit board, currently off getting fabricated by oshpark
    [reverse-engr.kicad_pcb, reverse-engr.sch]
2020-06-04 add a description of the mapping for wheel 1353909
    Obtained an ASCII Courier 10 DP PC (reorder number 1353909) and checked
    the character set. The first column is the printwheel address, the
    second column is the printed character, and the third column is the
    ASCII code. This printwheel will let me print a full ASCII character
    set on the wheelwriter.
    The difference between a standard wheelwriter typewheel and this one are
    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
2020-06-09 add some more traces and discussion
2020-06-13 more reverse engineering progress
    discovered the printer option board talks to the function board in terms
    of pseudo key press/releases. the key codes are included in
    doc/printwheel-map-with-option-board-codes.txt. See the bus traffic in
    doc/bus-traffic-chars.txt.
2020-06-27 discovered the paper-load lever switch generates 0x49 key event
